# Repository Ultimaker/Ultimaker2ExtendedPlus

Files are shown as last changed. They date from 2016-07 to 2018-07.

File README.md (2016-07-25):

# Ultimaker 2extended+
Bill of Materials and parts for Ultimaker 2extended+

In this repository you will find the documentation and source files for all parts in the Ultimaker 2extended+ 3D printer. In the Bill Of Materials (BOM) directory all the parts are numbered and named with the correct amounts and raw materials. 9407 is a subsystem, which has a separate BOM. 

The electronic files can be found in the following directories: 1155-F Print Table Heated Bed; 1249-B Ulticontroller board and 1546-A Ultimainboard V2.1.4.

If you are missing a part or information feel free to file an issue on github.

Harma Woldhuis <br>
Ultimaker Productmanager Hardware

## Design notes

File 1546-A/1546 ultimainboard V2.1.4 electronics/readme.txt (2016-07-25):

The UltiMainboard 2.x.x electronics are released under GPLv2 license.
And are based on the origonal Ultimaker electronics design by Jan-Jaap Schuurman, Siert Wijnia and ErikDeBruijn at http://reprap.org/wiki/Ultimaker's_v1.5.7_PCB
As well as the ArduinoMega2560 by Arduino: http://arduino.cc/en/Main/arduinoBoardMega2560

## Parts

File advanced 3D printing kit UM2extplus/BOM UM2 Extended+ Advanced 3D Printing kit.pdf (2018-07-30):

## 9522 UM2 Extended+ Advanced 3D Printing kit

Total quantity parts | 14
Partnummer | | Name | Quantity
1462 | A | door clip top | 2
1463 | A | door clip bottom | 2
1465 | A | door plate UM2+ ext | 1
1470 | A | build plate adhesion surface | 1
2152 | A | hex socket head remform screw 2.5 x 6 | 4
2278 | A | TFM Isolator Coupler | 2
2313 | C | olsson nozzle 0.40 | 2

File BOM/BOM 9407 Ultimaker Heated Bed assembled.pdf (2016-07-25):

## SubBOM

Total quantity parts | 39
Partnummer | Naam | Quantity | Material
1125 | A | Table Spring DR2150 | 3 | RVS 302
1153 | B | Print Table Base Plate | 1 | EN AW-6082
1155 | F | Print Table Heated Bed | 1 | several
1170 | B | Square Flanged Linear Bearing LMK12LUU | 2 | several
1183 | F | Heated Bed Cable | 1 | several
1187 | A | Trapezoidal Lead Nut | 1 | RG 7
1202 | B | ISO 7380 M3x10 | 6 | AISI 304
1206 | B | ISO 7380 M3x20 | 1 | AISI 304
1214 | A | ISO 7040 Nut M3 Prev. torque A2 | 4 | AISI 304
1217 | A | ISO 7380 M4x10 A2 | 8 | AISI 304
1243 | B | Heated Bed Cable Clip | 1 | ABS
1256 | A | Build Platform Glass Retainer Back | 2 | stainless steel
1257 | B | Knurled Nut Platform | 3 | RVS 304
1288 | A | Washer M6 | 3 | stainless steel
1987 | C | Table Clip Front-Left | 1 | RVS verenbandstaal AISI 301
1988 | C | Table Clip Front-Right | 1 | RVS verenbandstaal AISI 301

## 9407 Ultimaker Heated Build Platform Assembled

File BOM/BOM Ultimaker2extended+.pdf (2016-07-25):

9504

Total quantity
parts | 333
Partnummer | | Name | Quantity | Material
1011 | D | Y-linear shaft | 2 | 1.4034 (X46Cr13)
1012 | D | X-linear shaft | 2 | 1.4034 (X46Cr13)
1024 | E | Limit Switch, Black Short Wire | 1 | several
1056 | A | Sintered Bushing | 4 | Sintered Bronze
1065 | B | Linear Bearing LM6LUU | 2 | several
1069 | A | Tube Coupling Collet | 2 | Nylon
1071 | A | Clamp Clip | 2 | Nylon
1156 | A | Z-shaft Cap Bottom | 2 | PC ABS
1165 | B | Timing Pulley 5mm Shaft GT2 | 2 | Aluminum
1166 | C | Timing Pulley 8mm Shaft GT2 | 8 | Aluminum
1167 | E | Timing Pulley Double 8mm Shaft GT2 | 1 | Aluminum
1168 | B | Sliding Block Spring | 4 | DIN 17.223 material nr. 1.1200
1171 | B | Double flat Cable 10 Wire | 1 | several
1172 | A | Print Head Shaft X | 1 | 1.4034 (X46Cr13)
1173 | A | Print Head Shaft Y | 1 | 1.4034 (X46Cr13)
1176 | A | Spacer 8.2x10x5 | 2 | Nylon
1177 | A | Spacer 8.2x10x10 | 4 | Nylon
1178 | A | Spacer 8.2x10x25 | 1 | Nylon
1186 | E | Print Head Cable | 1 | several
1188 | A | Timing Belt GT2 200 | 2 | several
1189 | A | Timing Belt GT2 610 | 4 | several
1200 | A | ISO 7380 M3x8 | 4 | AISI 304
1201 | C | Washer Large M3 | 8 | AISI 304
1202 | B | ISO 7380 M3x10 | 16 | AISI 304
1203 | B | ISO 7380 M3x12 | 14 | AISI 304
1204 | B | ISO 7380 M3x16 | 44 | AISI 304
1205 | B | ISO 7380 M3x14 | 2 | AISI 304
1206 | B | ISO 7380 M3x20 | 1 | AISI 304
1207 | B | ISO 7380 M3x25 | 12 | AISI 304
1209 | C | Nut M3 | 5 | AISI 304
1213 | B | DIN 562 Square Nut M3 A2 | 40 | AISI 304
1214 | A | ISO 7040 Nut M3 Prev. torque A2 | 8 | AISI 304
1220 | A | Ball Bearing F688-2RS | 8 | stainless steel
1234 | F | Bottom Panel UM2 | 1 | dibond (Alu/PP/Alu)
1235 | E | Top Panel UM2 | 1 | dibond (Alu/PP/Alu)
1240 | C | Main Board Electronics Cover | 1 | Steel El.Galvanized
1241 | B | Motor Spacer UM2 | 2 | PC ABS
1242 | A | Spacer 3.2 x 6x 10 | 4 | Nylon
1244 | A | Knob Front UM2 | 1 | ABS 757
1245 | A | Knob Housing UM2 | 1 | PC 2807 Makrolon
1247 | A | Display Oled Blue | 1 | several
1249 | B | Ulticontroller Board | 1 | several
1250 | B | SD card 4G | 1 | several
1251 | B | Ulticontroller Electronics Cover | 1 | sheet metal DC01-A-m acc. EN10130
1255 | A | Sliding Block Half UM2 | 8 | PC ABS
1266 | C | Bowden tube | 1 | PFA
1279 | C | Feeder Ring | 1 | AISI 304
1281 | C | Braided Sleeve Clip | 5 | ABS

## Ultimaker2Extended+ voor assemblage

1287 | A | Washer M7 | 1 | AISI 304
1294 | A | Keep Hands Clear Sticker | 1 | plastic
1306 | C | Hot end holder bottom | 1 | ALU 3.2315
1307 | C | Hot end holder top | 1 | ALU 3.2315
1308 | C | Cooling Rib Hot End | 1 | ALU 3.2315
1310 | B | Hot end Isolator | 1 | AISI 303
1313 | A | Model Cooling Fan 12VDC 0.1 A | 2 | several
1315 | A | Jumper | 2 | several
1321 | C | Print Head Middle | 1 | PA6-GF30
1322 | D | Print Head Bottom | 1 | PA6-GF30
1325 | A | Insert material sticker | 1 | plastic
1326 | A | Warning sticker | 1 | plastic
1330 | C | Hot-end Cooling Fan 5VDC 0.08A | 1 | several
1348 | A | ISO 7380 M3x4 A2 | 4 | AISI 304
1351 | A | ISO 4762 M2,5x10 | 2 | AISI 304
1354 | A | ISO 724 Hex nut M7 | 1 | AISI 304
1362 | A | Tap Fix 2.5x14 mm staal verzinkt bolkop porzidrive | 8 | steel
1363 | A | Ferrite Core | 2 | Ferrite
1521 | A | Short Print Head Thumb Screw | 4 | steel
1546 | A | Ultimainboard V2.1.4 | 1
1748 | D | Print head top single hole | 1 | PA6-GF30
1960 | G | Grip Axis | 1 | AISI 303
1961 | A | Idler Spring | 1 | DIN 17.224 material nr. 1.4310
1962 | E | Tension Indicator | 1 | POM-GF10
1963 | N | Feeder casing Part A-left | 1 | POM-GF10
1965 | N | Feeder casing Part B-left | 1 | POM-GF10
1967 | M | Feeder lever part A | 1 | POM-GF10
1968 | J | Feeder lever part B | 1 | POM-GF10
1969 | F | spur gear 1M 11T | 1 | PA6
1970 | E | spur gear 1M 36T | 1 | PA6
1971 | C | Threaded standoff | 2 | AISI 304
1972 | C | idler wheel | 1 | AISI 303
1973 | A | bearing idler wheel | 1 | stainless steel
1974 | A | bearing feeder axis | 2 | stainless steel
1976 | D | Filament Guide Insert | 1 | POM-GF10
1977 | B | Feeder Motor | 1 | several
2048 | A | Din 914 M4x4 Set screw | 11 | AISI 304
2201 | F | Z-linear shaft | 2 | 1.4034 (X46Cr13)
2202 | A | Z-Motor with Trapezoidal Lead Screw | 1 | several
2203 | B | X,Y motor | 2 | several
2204 | B | Limit Switch, Blue Wire | 1 | several
2205 | B | Limit Switch, Red Wire | 1 | several
2206 | A | LED Strip Cold white | 1 | several
2211 | H | Back Panel | 1 | dibond (Alu/PP/Alu)
2212 | A | Left Panel | 1 | dibond (Alu/PP/Alu)
2213 | A | Right Panel | 1 | dibond (Alu/PP/Alu)
2214 | B | Front Panel | 1 | dibond (Alu/PP/Alu)
2222 | A | Cable Cover | 2 | Staalplaat DC01-A-m vlg. EN 10130
2275 | C | Isolator Spacer 9.4 mm | 1 | Alu type 5000 or 6000
2278 | A | TFM Isolator Coupler | 1 | TFM
2283 | C | Heater Cartridge 24V 35W | 1 | several
2284 | B | Fan Bracket | 1 | AISI 304
2287 | B | Print Table Back Cover | 1 | dibond (Alu/PP/Alu)
2288 | B | PT 100B sensor glassfiber | 1 | several
2311 | E | olsson heater block | 1 | brass MS58
2313 | C | olsson nozzle 0.40 | 1 | brass MS58

2317 | B | M3x16 countersunk pozidrive | 1 | AISI 304
2322 | A | Nozzle ring DIN 6798V M3 | 1 | AISI 304
9129 | A | SD card sticker | 1 | plastic
9407 | A | Ultimaker Heated Build Platform Assembled | 1 | several

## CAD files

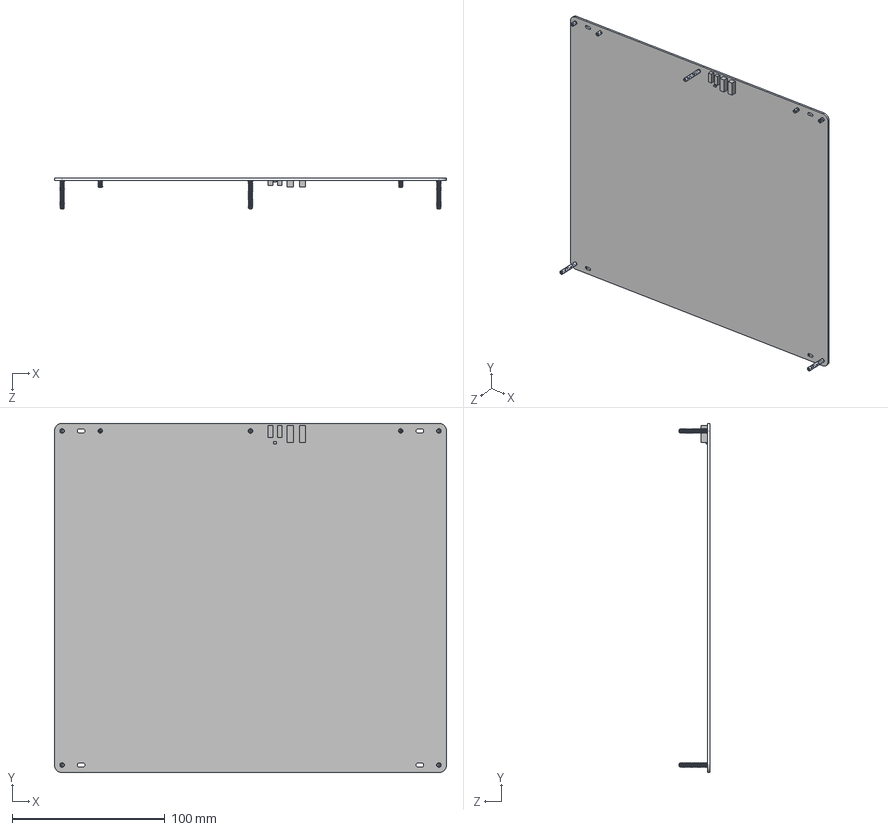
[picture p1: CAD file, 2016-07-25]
1155-F/1155-F.STEP
257.0 x 229.0 x 20.0 mm
1155-D
FH-M3-xZI_FH-M3-6ZI x 4
FH-M3-xZI_FH-M3-20ZI x 3

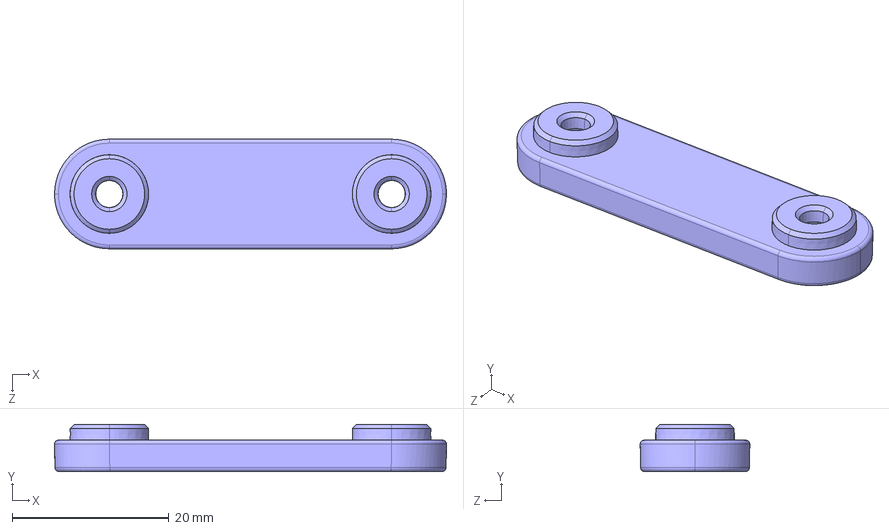
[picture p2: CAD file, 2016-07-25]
1156-A.STEP
50.0 x 6.00 x 14.0 mm

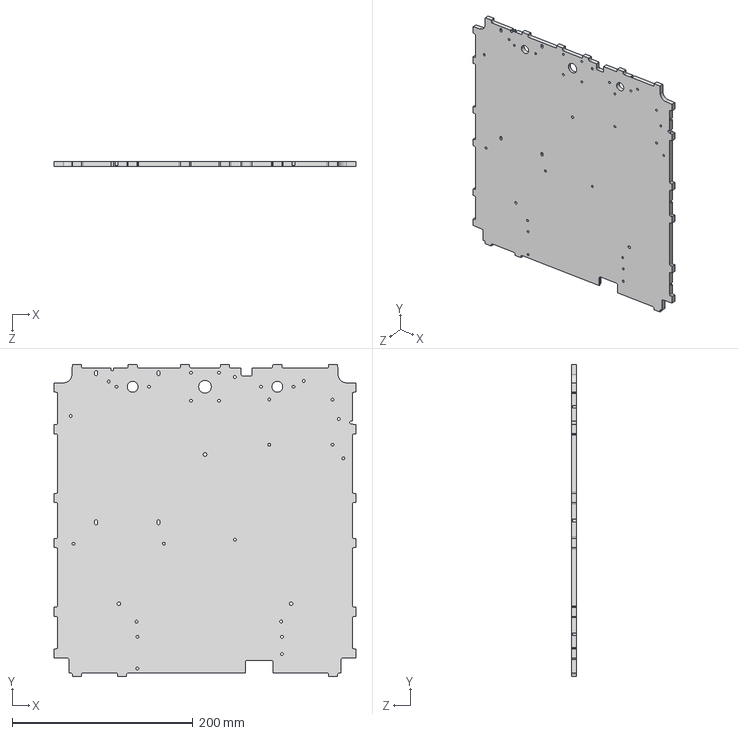
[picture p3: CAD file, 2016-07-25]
1234-F/1234-F.STEP
334.2 x 345.6 x 6.00 mm

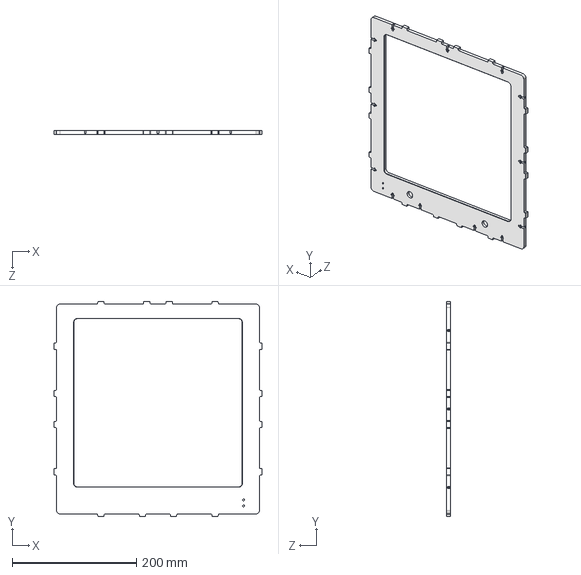
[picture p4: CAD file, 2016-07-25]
1235-E/1235-E.STEP
334.2 x 345.6 x 6.00 mm

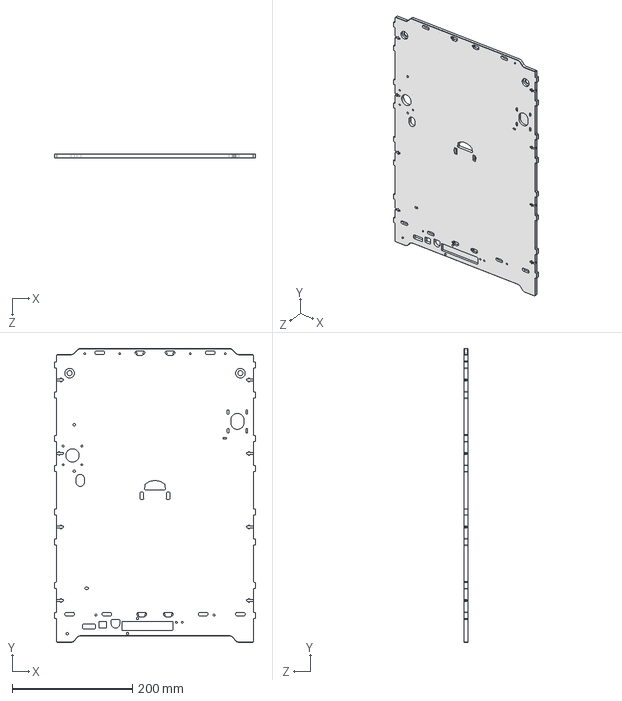
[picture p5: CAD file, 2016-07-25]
2211-H/2211-H.STEP
334.2 x 488.0 x 6.00 mm

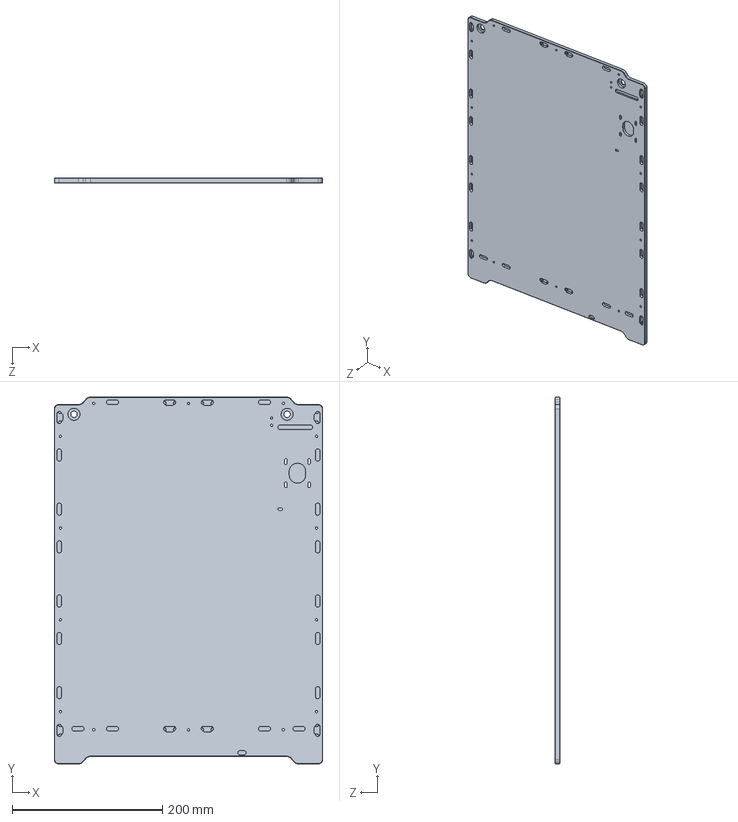
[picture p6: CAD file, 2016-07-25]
2212-A/2212-A.STEP
357.0 x 488.0 x 6.00 mm

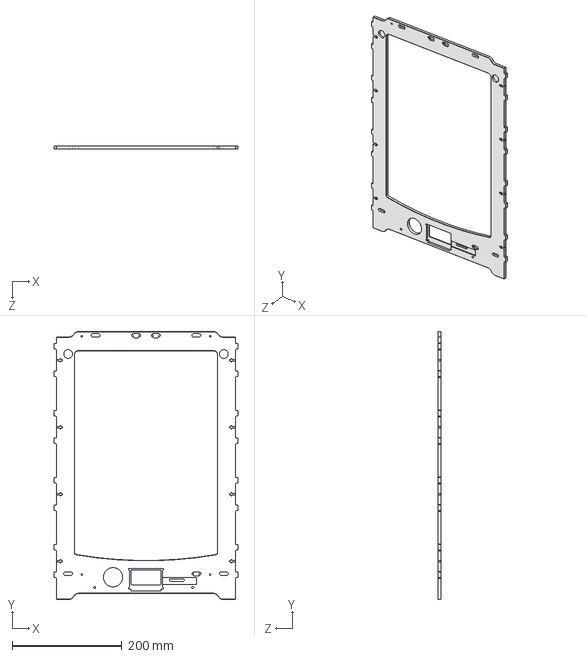
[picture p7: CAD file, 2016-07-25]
2214-B/2214-B.STEP
334.2 x 488.0 x 6.20 mm

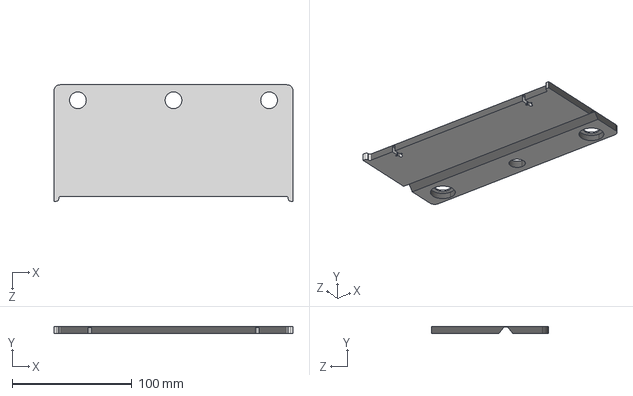
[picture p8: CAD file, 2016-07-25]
2287-B/2287-B.STEP
200.0 x 6.10 x 97.5 mm

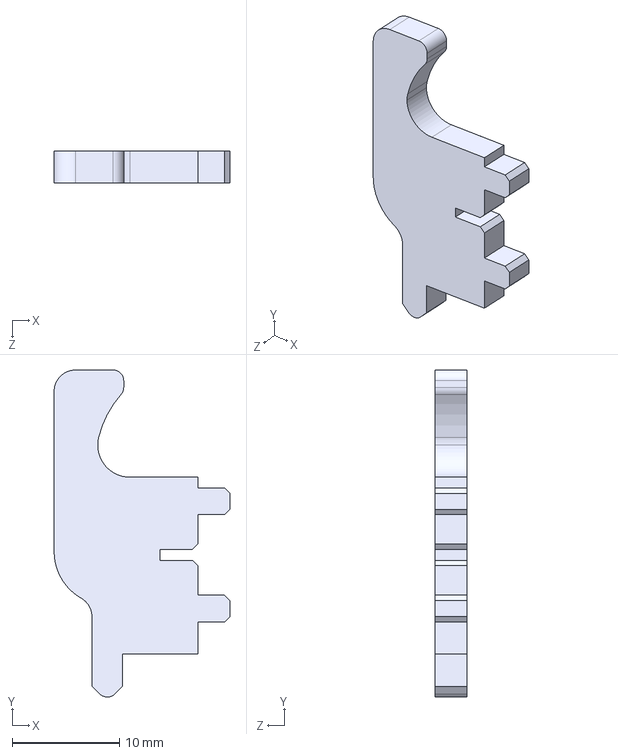
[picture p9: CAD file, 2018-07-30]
advanced 3D printing kit UM2extplus/1462/1462-A.STEP
16.4 x 30.5 x 3.00 mm

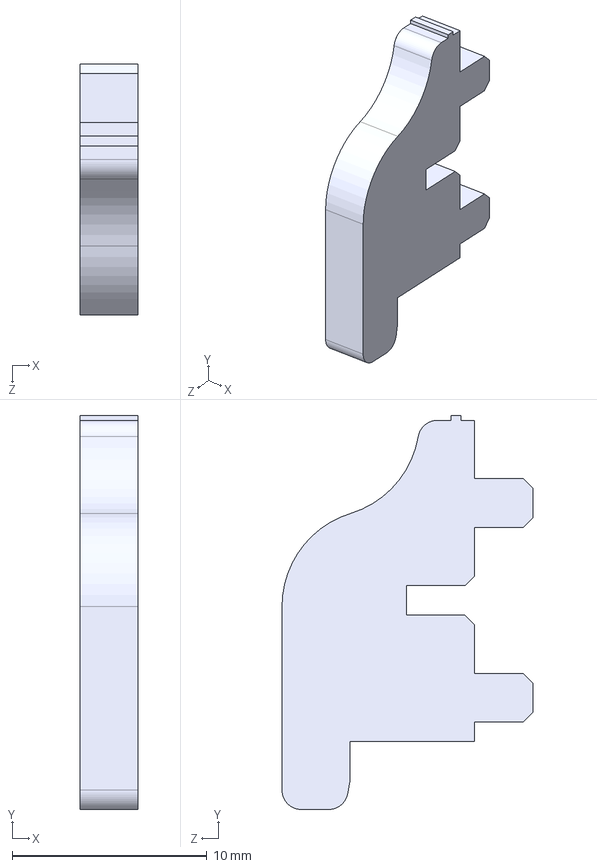
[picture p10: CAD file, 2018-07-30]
advanced 3D printing kit UM2extplus/1463/1463-A .STEP
3.00 x 20.3 x 12.9 mm

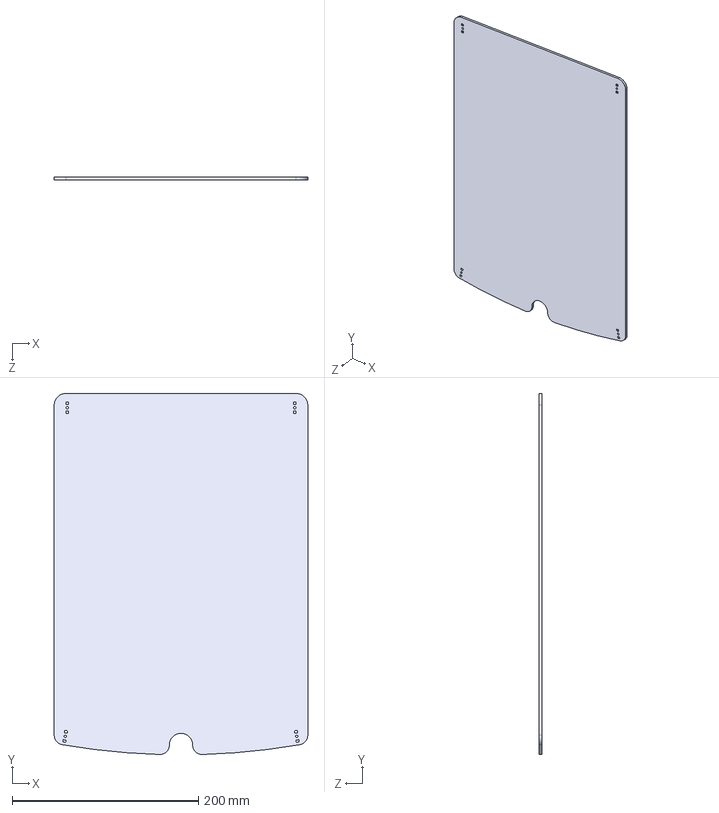
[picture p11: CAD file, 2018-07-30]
advanced 3D printing kit UM2extplus/1465/1465-A .STEP
272.0 x 387.2 x 3.00 mm

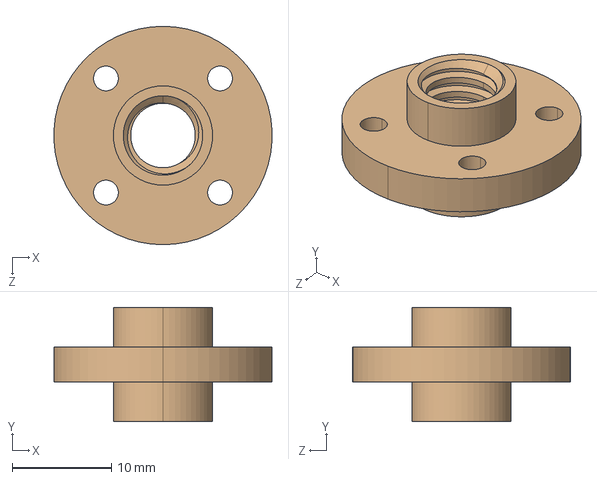
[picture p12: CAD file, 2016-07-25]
1187-A.STEP
22.0 x 11.5 x 22.0 mm

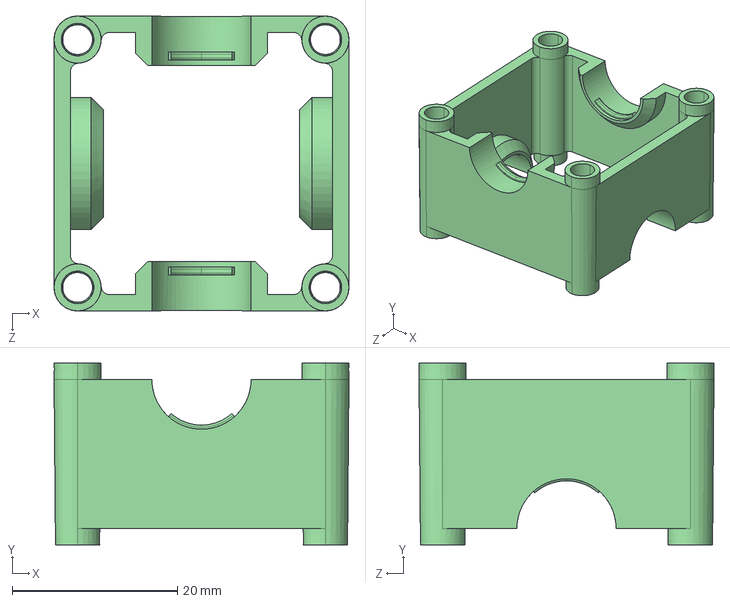
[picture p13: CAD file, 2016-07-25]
1321-C.STEP
35.7 x 22.0 x 35.7 mm

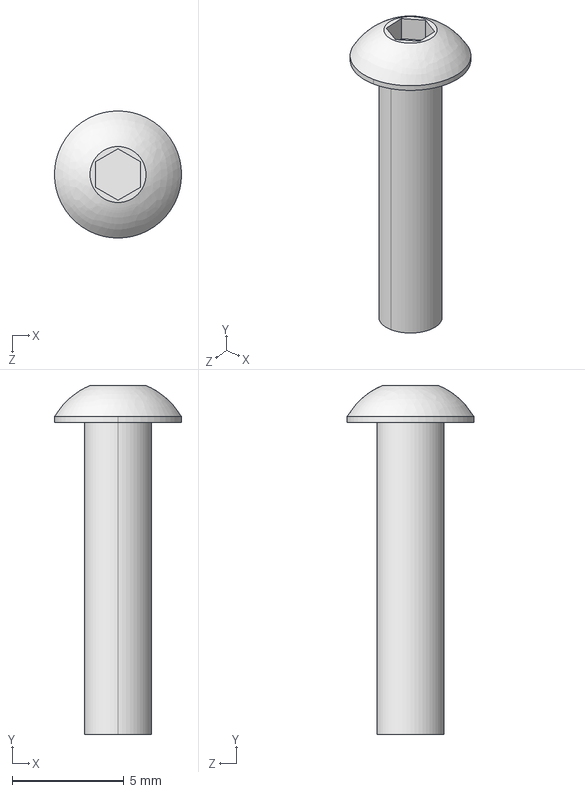
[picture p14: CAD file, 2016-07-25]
1205-B.STEP
5.70 x 15.6 x 5.70 mm

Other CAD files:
2213-A/2213-A.STEP
1279-C.STEP
1165-B.STEP
1308-C.STEP
1011-D.STEP
1012-D.STEP
1024-E.STEP
1056-A.STEP
1065-B.STEP
1069-A.STEP
1071-A.STEP
1125-A.STEP
1153-B.STEP
1166-C.STEP
1167-E.STEP
1168-B.STEP
1170-B.STEP
1172-A.STEP
1173-A.STEP
1176-A.STEP
1177-A.STEP
1178-A.STEP
1183-F.STEP
1188-A.STEP
1189-A.STEP
1200-A.STEP
1201-C.STEP
1202-B.STEP
1203-B.STEP
1204-B.STEP
1206-B.STEP
1207-B.STEP
1209-C.STEP
1213-B.STEP
1214-A.STEP
1217-A.STEP
1220-A.STEP
1234-F/1234-F.DXF
1235-E/1235-E.DXF
1240-C.STEP
1241-B.STEP
1242-A.STEP
1243-B.STEP
1244-A.STEP
1245-A.STEP
1247-A.STEP
1250-B.STEP
1251-B.STEP
1255-A.STEP
1256-A.STEP
1257-B.STEP
1266-C.STEP
1281-C.STEP
1287-A.STEP
1288-A.STEP
1294-A.STEP
1306-C.STEP
1307-C.STEP
1310-B.STEP
1313-A.STEP
1315-A.STEP
1322-D.STEP
1330-C.STEP
1348-A.STEP
1351-A.STEP
1354-A.STEP
1362-A.STEP
1363-A.STEP
1521-A.STEP
1748-D.STEP
1960-G.STEP
1961-A.STEP
1962-E.STEP
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

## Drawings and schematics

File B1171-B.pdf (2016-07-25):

# Ultimaker Original

## Heat shrink to protect

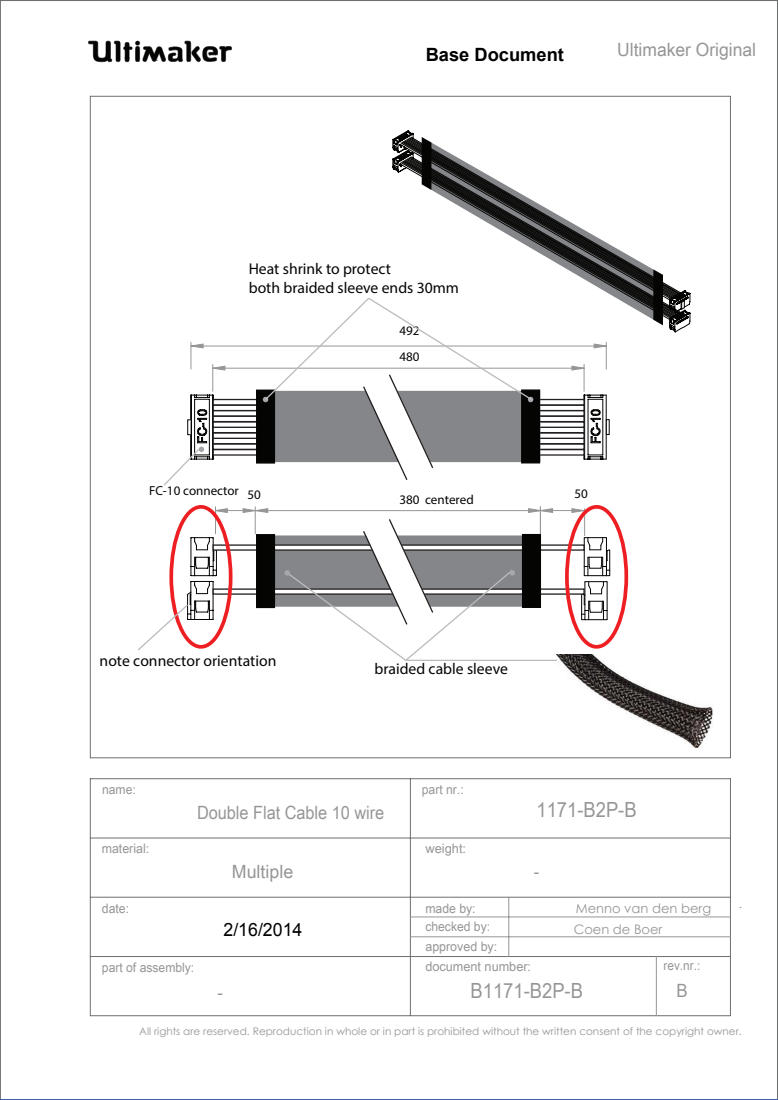
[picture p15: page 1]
Multiple; name:; material:; date:; part of assembly:; rev.nr.:; part nr.:; made by:; weight:; approved by:; checked by:; document number: B1171-B2P-B; 380 centered; FC-10 connector; Base Document

both braided sleeve ends 30mm

note connector orientation

braided cable sleeve

Double Flat Cable 10 wire

Menno van den berg
Coen de Boer

All rights are reserved. Reproduction in whole or in part is prohibited without the written consent of the copyright owner.

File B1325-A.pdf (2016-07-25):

## Spec. Sheet

33 mm

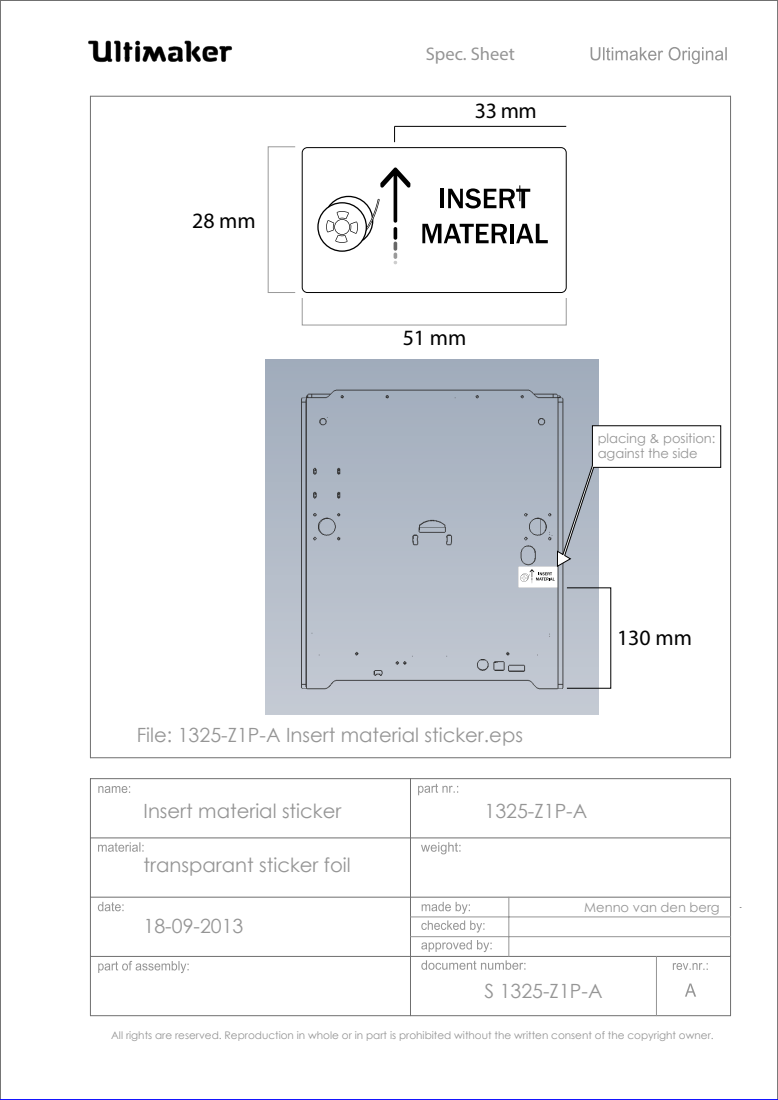
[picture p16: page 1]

placing & position:
against the side

File: 1325-Z1P-A Insert material sticker.eps

Insert material sticker

transparant sticker foil

Menno van den berg

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

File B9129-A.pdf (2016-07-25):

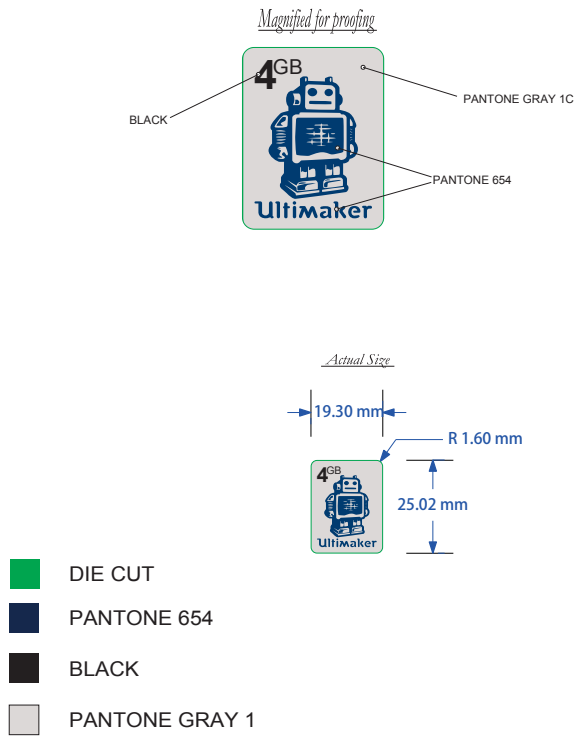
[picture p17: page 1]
DIE CUT; PANTONE 654; BLACK; PANTONE GRAY 1C; PANTONE GRAY 1

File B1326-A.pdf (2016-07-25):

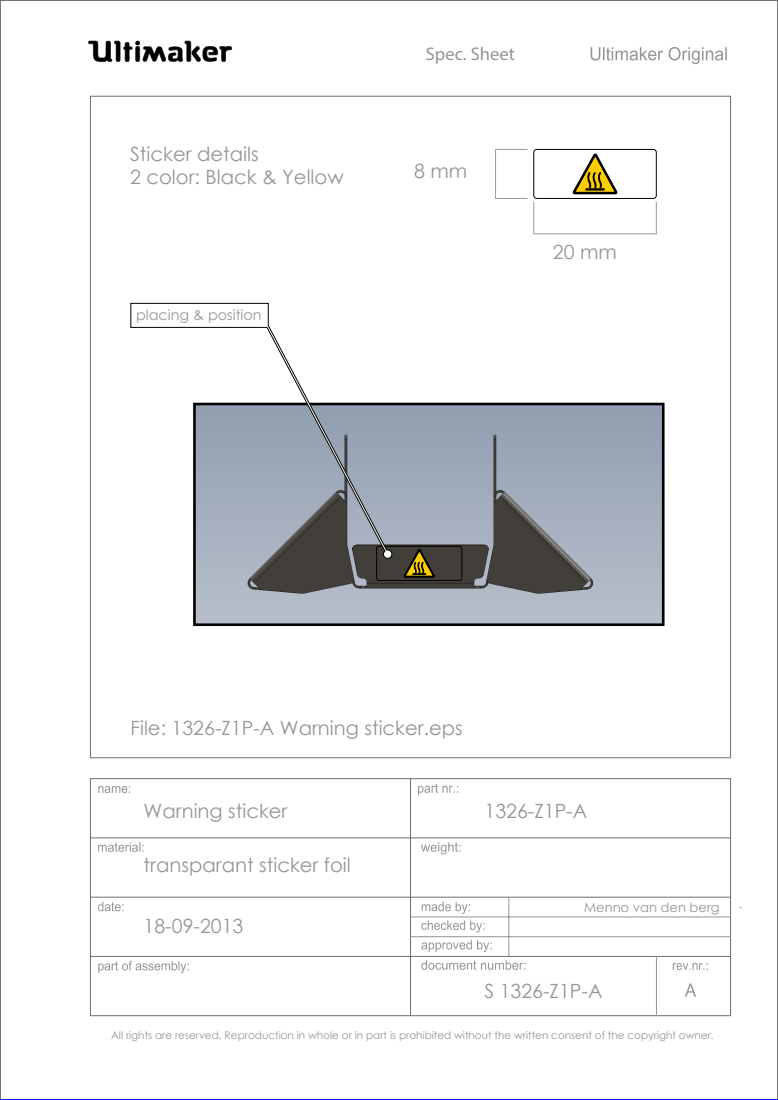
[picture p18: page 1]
Spec. Sheet; Warning sticker; placing & position

Sticker details
2 color: Black & Yellow

File: 1326-Z1P-A Warning sticker.eps

transparant sticker foil

Menno van den berg

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

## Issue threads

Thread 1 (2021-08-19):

Ultimaker 2 Extended + code

WissamKdotcom, 2021-08-19:
Hello,

I have a tiny edit I want to do to the code of my printer's firmware, UM2E+, but when I use Ultimaker2Marlin code, my steppers start vibrating like crazy, in a way that suggests that they have insufficient torque. So basically that code is unusable. I looked into it some more and found out that I should edit twi.c file in Arduino before compiling, and I did but that didn't change anything. So I'm guessing that code doesn't work for my UM2E+. I expected that I should find the code here but it doesn't exist here either. Help?

PS. I barely know about programming so excuse my possible terminology mistakes.

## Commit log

2016-07-25 initial commit
    initial commit
    [1011-D.STEP, 1012-D.STEP, 1024-E.STEP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]
2018-07-30 advanced 3Dprinting kit
    added files
    [1462-A.DXF, 1462-A.STEP, 1463-A .DXF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]
